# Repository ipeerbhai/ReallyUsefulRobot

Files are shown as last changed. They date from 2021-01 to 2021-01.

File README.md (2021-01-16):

# ReallyUsefulRobot

## Hardware

CAD files are provided in STEP/STP format. This is the whole assembly as a solid format so you can easily edit it. You will need to load it into some CAD software and edit/export individual STLs for printing.

Tyres are printed in TPU, I used Ninjaflex. The rest in PLA printed with a combination of 0.5mm and 1.2mm nozzles.

Motors are 6374 150Kv BLDC motors from the ODrive store: https://odriverobotics.com/shop
Encoders and cables are the 8192 CPR encoders also from the ODrive store.
I used a 56V ODrive 3.6, the robot runs from a 24V LiPo, but it can be 25V+ when it's charged.
Wheel Drive belts are 590mm T5 12mm wide PU belts with steel tensioners made by Synchroflex.
'Utility Stick' drive belt is an HTD 5mm pitch 15mm wide 1790mm length belt.

Other electronics so far include:

-Teensy 4.1
-NVIDIA Xavier NX / Jetson Nano 4gb
-RPLIDAR A2
-24v and 11.1v lipos, switches and wiring etc

## BOM

This is a work-in-progress partial BOM of the parts needed to build one of these bots in different regions.

### Wheel assembly
The wheel assembly consists of the following parts:

* Main axle -- one of either: Misumi FABSP20-454 (metric), or (imperial) cut2size metals (https://www.cut2sizemetals.com/stainless-steel/threaded%E2%88%92rod/141/) 3/4-10 (diameter, thread pitch), 17 7/8" long.
* Wheel bushings -- 4x Igus iglide RFM-2023-21 20mm plastic bushings might work, or these can be 3d printed to chosen axle.
* Wheel bearings -- 4x vxb Bearing 6005zz (different seals are available -- the zz looks like the easiest to source.)

### Base
* T-Slot Re-enforcement -- 2x OpenBuilds 2060 extrusion 250mm long (available in either black or clear anodized)
* T-Slot "neck" -- 1x OpenBuilds 2080 extrusion, 1000mm long?
* The "neck" motor seems to be a Gimson Robotics GR-WM2 (2019 version)

### Head

## Software

Obviously this isn't a comprehensive guide to ROS, you will need to undestand some core concepts before building this. The Robot runs ROS Melodic on Ubuntu 18.04. This is because the NVIDIA Xavier NX runs 18.04 by default.

On the robot:

The arduino code runs on the Teensy 4.1. This talks to the wheel encoders. It subscribres to the cmd_vel topic and publishes Odom, and TF for the robot's motions. The RPLIDAR A2 node publishes the scan topic: https://github.com/robopeak/rplidar_ros

The Teensy also talks to the ODrive on Serial1. In order to get the ROS Serial library running on the Teensy 4.1, and get both the ROS Serial library and the ODrive library to run together I had to make various modifications. I removed mentions of the Stream Operator which were in the original ODrive Arduino example: https://github.com/madcowswe/ODrive/tree/master/Arduino/ODriveArduino/examples/ I also had to modify the ROS Serial library to add Teensy 4.1 support, and increase buffers so that the Odom message could be published over Serial. I've included both modified libraries as zip files.

The 'rur' and 'rur_description' ROS packages are installed on the robot, and everything is launched with the 'rur_bringup.launch' file. This launches the ROS Serial node to talk tot he Teensy 4.1, starts the laser, and also uses the Robot & Joint State Publishers to publish the transform in the URDF file so the laser is linked to the robot base in the right place.

On my remote workstation:

The 'rur_navigation' ROS package is installed on the remote workstation (although it could be run locally). You will also need to install the ROS navigation stack and slam_gmapping. You will also need to run rosdep to install any other dependencies: http://wiki.ros.org/rosdep

https://github.com/ros-planning/navigation/tree/melodic-devel
https://github.com/ros-perception/slam_gmapping/tree/melodic-devel

There is no launch file for gmapping, so having launched the rur_bringup package on the robot and launched Gmapping ( rosrun gmapping slam_gmapping scan:=scan ) you'll have to open Rviz and manually add/connect the topics for TF/Laser/Map etc. You can use the map server/saver command to save the map ( rosrun map_server map_saver -f ~/map )

After the map is complete you can launch the rur_navigation package which will open Rviz automatically. Use: roslaunch rur_navigation rur_navigation.launch map_file:=$HOME/map.yaml   to connect to the map you saved.

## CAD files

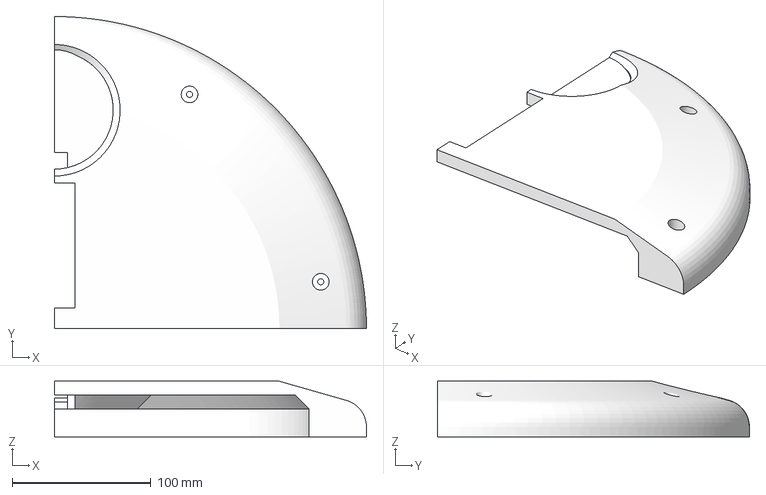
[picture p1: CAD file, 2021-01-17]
CAD/PrintableParts/BaseAssembly/RightFrontCoverPlate.3mf
224.8 x 224.8 x 40.0 mm

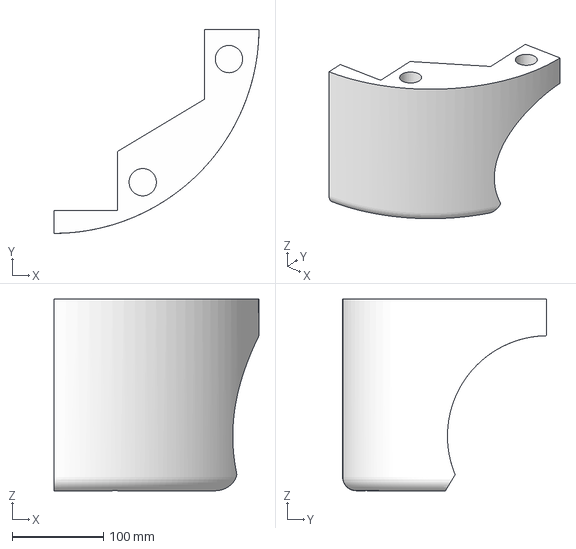
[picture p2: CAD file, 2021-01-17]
CAD/PrintableParts/PrusaI3Printable/BaseAssembly/RightRearFender.3mf
224.8 x 223.5 x 210.0 mm

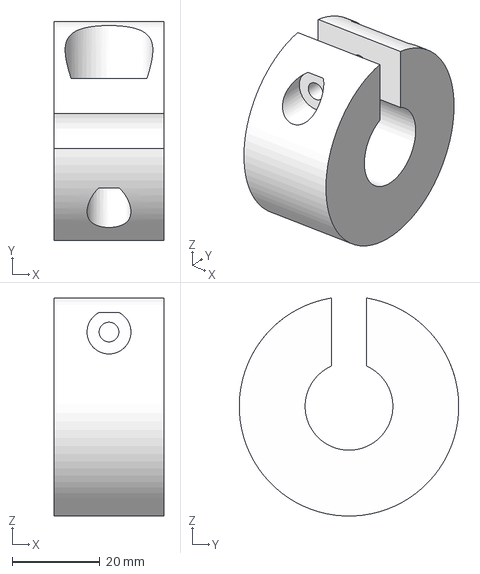
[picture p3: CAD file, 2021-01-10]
CAD/PrintableParts/PrusaI3Printable/WheelAssembly/WheelClamp.3mf
25.0 x 50.0 x 49.7 mm

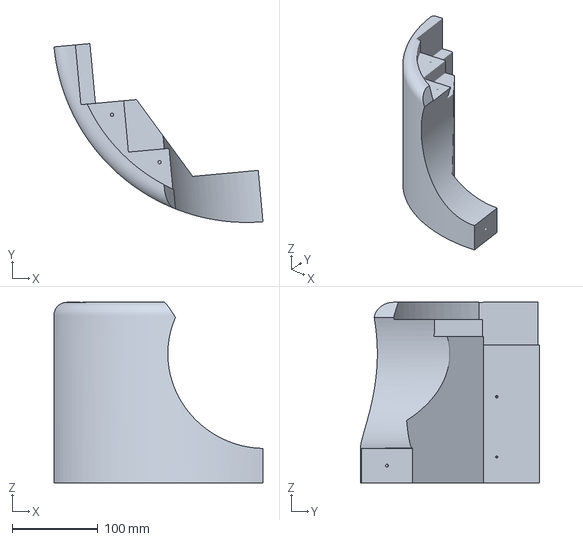
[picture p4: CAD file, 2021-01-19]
CAD/PrintPlatters/RightFrontFender_1.3mf
243.1 x 208.0 x 210.0 mm

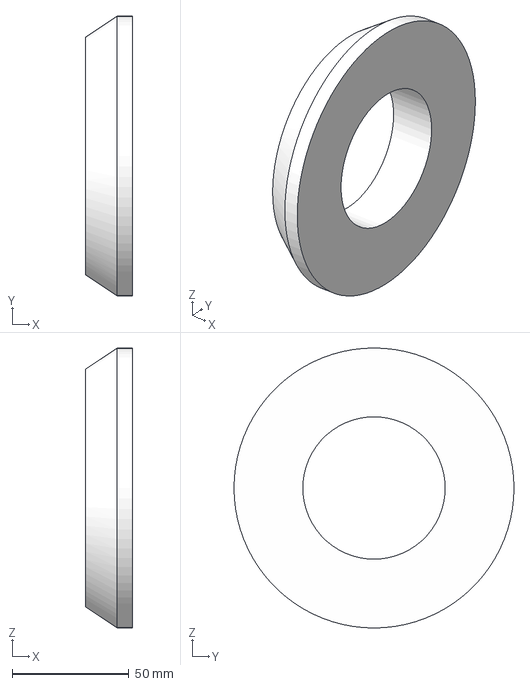
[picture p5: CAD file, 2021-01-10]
CAD/PrintableParts/PrusaI3Printable/WheelAssembly/HubPart2.3mf
20.0 x 120.0 x 120.0 mm

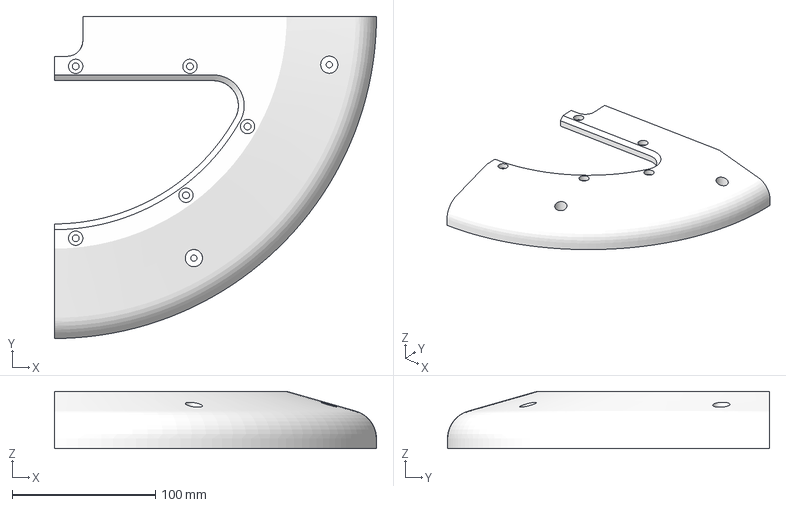
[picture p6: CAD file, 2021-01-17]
CAD/PrintableParts/BaseAssembly/RightReadCoverPlate.3mf
224.8 x 224.8 x 40.0 mm

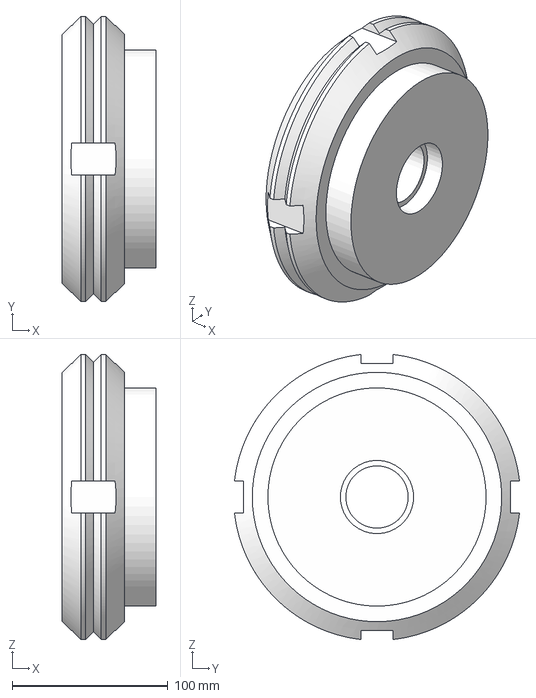
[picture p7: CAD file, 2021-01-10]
CAD/PrintableParts/PrusaI3Printable/WheelAssembly/HubPart1.3mf
60.0 x 182.9 x 182.9 mm

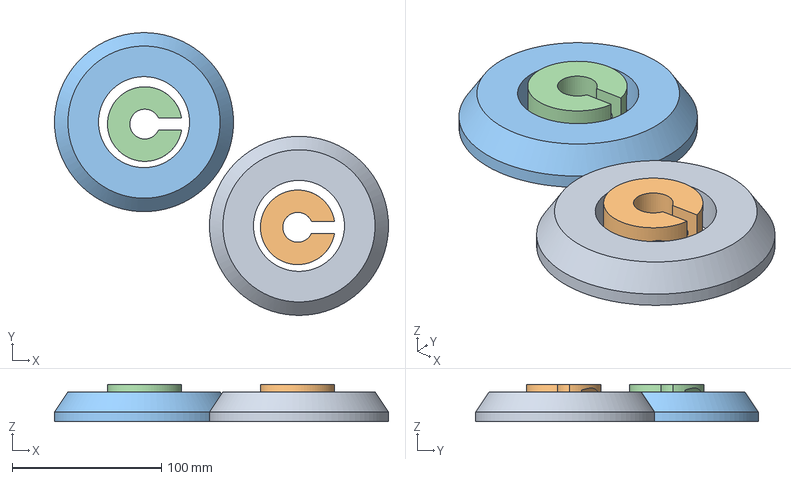
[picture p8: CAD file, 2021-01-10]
CAD/PrintPlatters/WheelPlatter1.3mf
223.9 x 189.5 x 25.0 mm
HubPart2_1 x 2
WheelClamp_1 x 2

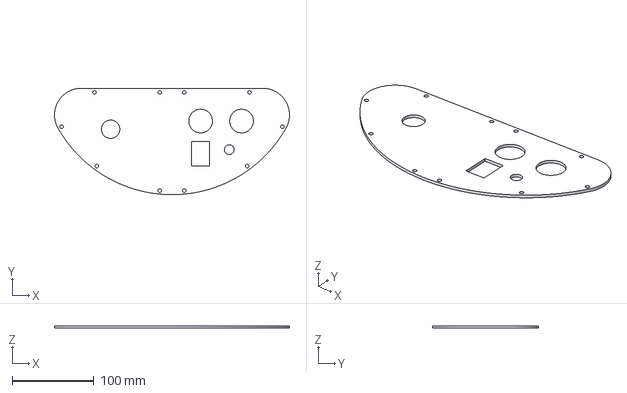
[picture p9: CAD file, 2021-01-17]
CAD/PrintableParts/BaseAssembly/TopInstrumentPanel.3mf
287.2 x 130.0 x 3.00 mm

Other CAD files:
CAD/PrintableParts/BaseAssembly/LeftFrontFender.3mf
CAD/PrintableParts/PrusaI3Printable/BaseAssembly/LeftFrontFender.3mf
CAD/PrintPlatters/LeftFrontFender_1.3mf
CAD/PrintableParts/PrusaI3Printable/BaseAssembly/RightFrontFender.3mf
CAD/PrintableParts/PrusaI3Printable/BaseAssembly/LeftRearFender.3mf
CAD/PrintableParts/BaseAssembly/LeftRearFender.3mf
CAD/PrintableParts/BaseAssembly/LeftFrontCoverPlate.3mf
CAD/PrintableParts/BaseAssembly/LeftRearCoverPlate.3mf
CAD/PrintableParts/BaseAssembly/RightFrontFender.3mf
CAD/PrintableParts/BaseAssembly/RightRearFender.3mf

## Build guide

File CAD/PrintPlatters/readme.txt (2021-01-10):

This directory contains some of the parts "platterized" for a 250mm x 250mm bed 3d printer (like a prusa, as that's what I have).
Some parts, like the Tires, are not fun to print.  Those have been sent to a bureau instead, and are not platterized.

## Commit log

2021-01-10 BOM so far.
2021-01-10 Getting a platter ready to print on my prusa mk3s
    [HubPart1.3mf, HubPart2.3mf, WheelClamp.3mf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]
2021-01-16 work in progress -- attempting to create a BOM.
2021-01-17 Trying to make a printable version, but parts too large for my prusa i3.
    [HubPart1.3mf, HubPart2.3mf, LeftFrontCoverPlate.3mf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]
2021-01-17 Modified parts to use alignment pins, be slightly smaller to print on a Prusa i3 mk3.
    [LeftFrontFender.3mf, LeftRearFender.3mf, RightFrontFender.3mf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]
2021-01-17 WIP: Beginning print of fender, ETA 16h with 0.4mm nozzle.
    [LeftFrontFender_1.3mf]
2021-01-19 platterized the right front fender for prusa i3.
    [RightFrontFender_1.3mf]
